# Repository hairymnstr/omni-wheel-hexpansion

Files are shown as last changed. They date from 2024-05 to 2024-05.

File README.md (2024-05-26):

# Motor Hexpansion / Omni Wheel Hexpansion

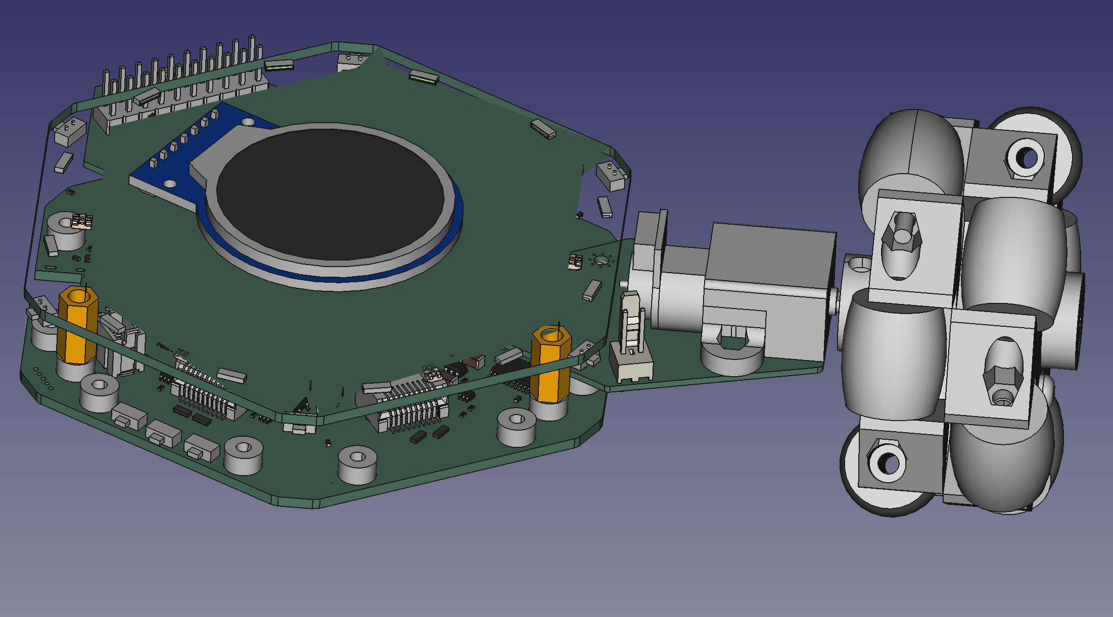
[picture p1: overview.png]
An omni wheel attached to a group of circuit boards all rendered in 3D CAD


This project is a "hexpansion" for the [EMF Camp Tildagon badge](https://tildagon.badge.emfcamp.org/).
It adds a motor driver, encoder reader and mounting points for an N20 motor.  The motor is mounted
straight out from the slot the hexpansion is mounted in.  By installing 3 of these hexpansions and
programming the badge appropriately you should be able to make it rotate or move in any direction
desired.

# Things you need to make a complete Omni Wheel Hexpansion

1. A Motor Hexpansion board as described in the kicad\_project folder
2. A 60mm Omni Wheel, see [my Omni Wheel repository](https://github.com/hairymnstr/OmniWheel) for a 3D printable design
3. A 110:1 geared micro metal motor with extended back shaft [COM0818 from Pimoroni](https://shop.pimoroni.com/products/micro-metal-gearmotor-extended-back-shaft?variant=39421592043603)
4. A long mounting bracket for the motor [COM0817 from Pimoroni](https://shop.pimoroni.com/products/long-micro-metal-gearmotor-bracket-pair?variant=39861109850195)
5. An encoder for the motor [PIM604 from Pimoroni](https://shop.pimoroni.com/products/micro-metal-motor-encoder?variant=39888423321683)
6. A JST-SH 6 way cable to connect the encoder/motor to the hexpansion [CAB1009 from Pimoroni](https://shop.pimoroni.com/products/jst-sh-cable-6-pin?variant=39292536455251)
7. A couple of short M2 bolts to secure the hexpansion to your badge [M2 x 5mm Torx Pan head bolt](https://www.westfieldfasteners.co.uk/Bolts_Screws_Metric/Torx_Pan_Screw_M2x5_A2_Stainless.html)

You'll need 3 of each part to make a complete hexpansion.

# Programming the hexpansion

To program a blank hexpansion I used the Raspberry Pi debug probe [(available from Pimoroni)](https://shop.pimoroni.com/products/raspberry-pi-debug-probe?variant=40511574999123).
The probe can be connected to both the SWD pins and the UART for test and debug.  The firmware
is also in this repository and can be built easily using Visual Studio Code or just by running
the Makefile provided you have an ARM embedded compiler installed.

# Hexpansion API

The hexpansion has a very simple interface, everything is controlled via I2C.

There are 2 devices presented (both in software on the STM32):

* 0x50 is a 256 byte fake EEPROM which has a valid "hexpansion" header identifying the board
* 0x42 has a register based control and status interface

Both devices operate in "memory" mode, i.e. they take an address then data to be read or written.
Both use single byte addressing.  Using the Micropython `readfrom_mem` and `writeto_mem` functions
will work.

There are only 2 registers defined, they can both be read and written, reading or writing any
other part of the 256 byte address space will be stored but won't make any difference to the
operation of the device.  Reads are guaranteed to be coherent so you won't get part of a register
that's updated between starting the I2C transaction and finishing it.

* Address 0, length 16 bit little endian: PWM value, a value in the range -100 to 100
* Address 2, length 16 bit little endian: Encoder position

Using the badge software you can use `machine.I2C` and `struct` to access these registers.
Note that on the Tildagon badge there are I2C buses for each hexpansion so you will need
to change the paramter to `I2C` for each slot you connect to.

This trivial example sets the speed to full reverse then prints out the current
encoder value.

    import struct
    import machine

    bus = machine.I2C(2)
    bus.writeto_mem(0x42, 0, struct.pack("<h", -100))
    print(struct.unpack("<h", bus.readfrom_mem(0x42, 2, 2))[0])

# Questions I think might be asked
## Why all the fuss about encoders?

Well originally I was planning a pen holding hexpansion as well and making a floor-turtle type
system.  To get any kind of accurate and repeatable motions I needed to know how far the wheels
were actually turning as there are variations between motors especially when under load.

## What's the point of the external MCU?

You could drive the motor driver and maybe do the encoder reading all from the MCU on the badge
itself.  But, I wanted to make sure I as catching all that encoder information on all three
motors.  To do that I decided a dedicated encoder controller would be good but couldn't find
one.  I also looked at using an I2C H-Bridge and adding an I2C EEPROM for board identification
and realised using one of the very cheap STM32G0 MCUs I could emulate an EEPROM and make an I2C
controlled motor driver and have a dedicated hardware encoder interface all in one.

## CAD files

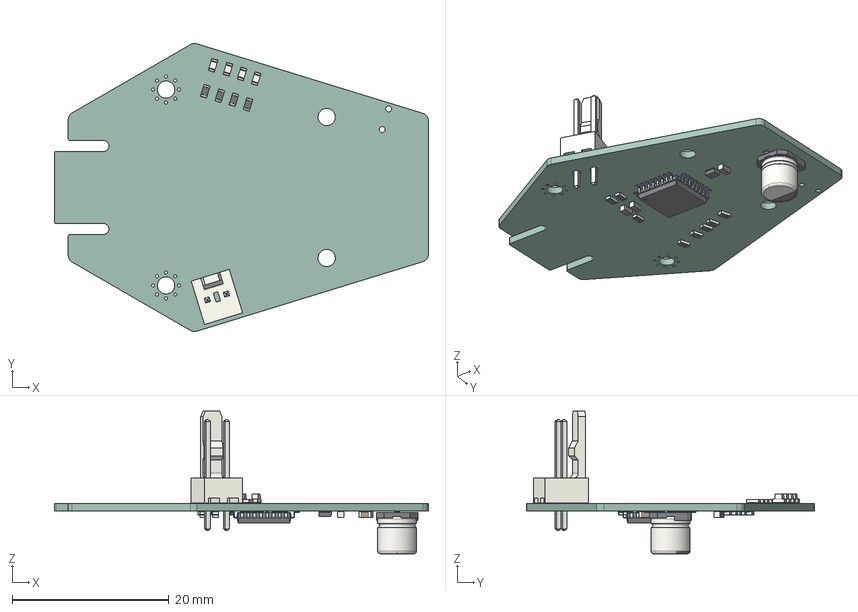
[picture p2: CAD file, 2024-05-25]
manufacturing/motor_hexpansion.step
47.8 x 36.8 x 18.2 mm
LED_0603_1608Metric x 4
R_0603_1608Metric x 12
Molex_AE_6410_02A
CP_Elec_5x54
LQFP_32_7x7mm_P08mm
C_0603_1608Metric x 4
SOT_563
motor_hexpansion_PCB

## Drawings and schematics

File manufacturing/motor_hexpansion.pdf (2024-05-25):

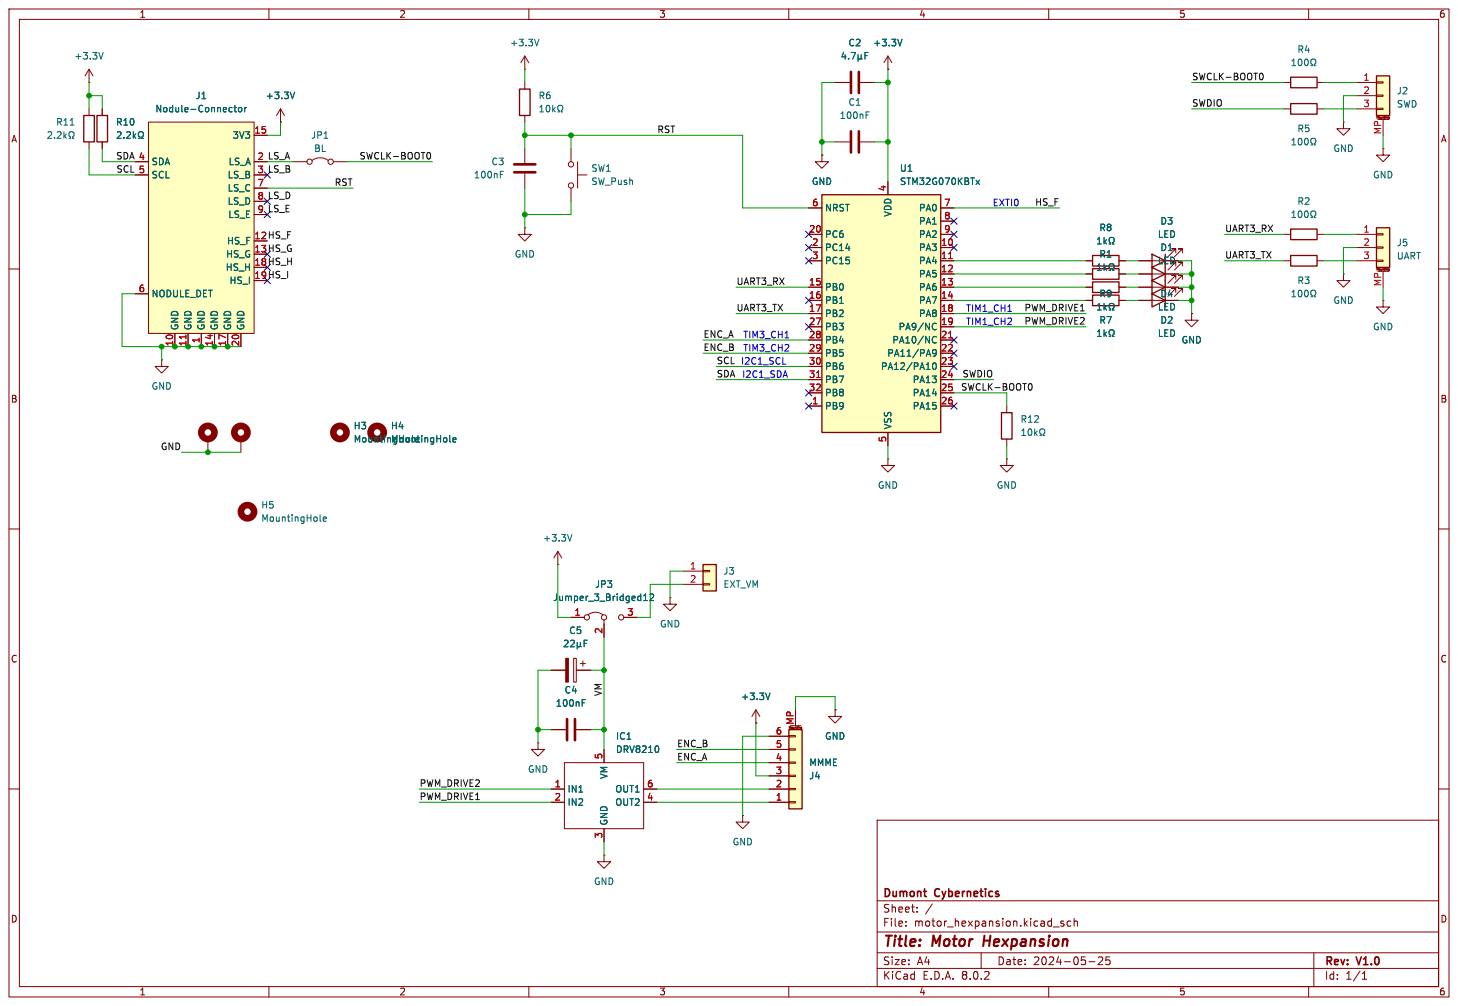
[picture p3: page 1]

File: motor_hexpansion.kicad_sch Sheet: / Dumont Cybernetics

Id: 1/1 Title: Motor Hexpansion

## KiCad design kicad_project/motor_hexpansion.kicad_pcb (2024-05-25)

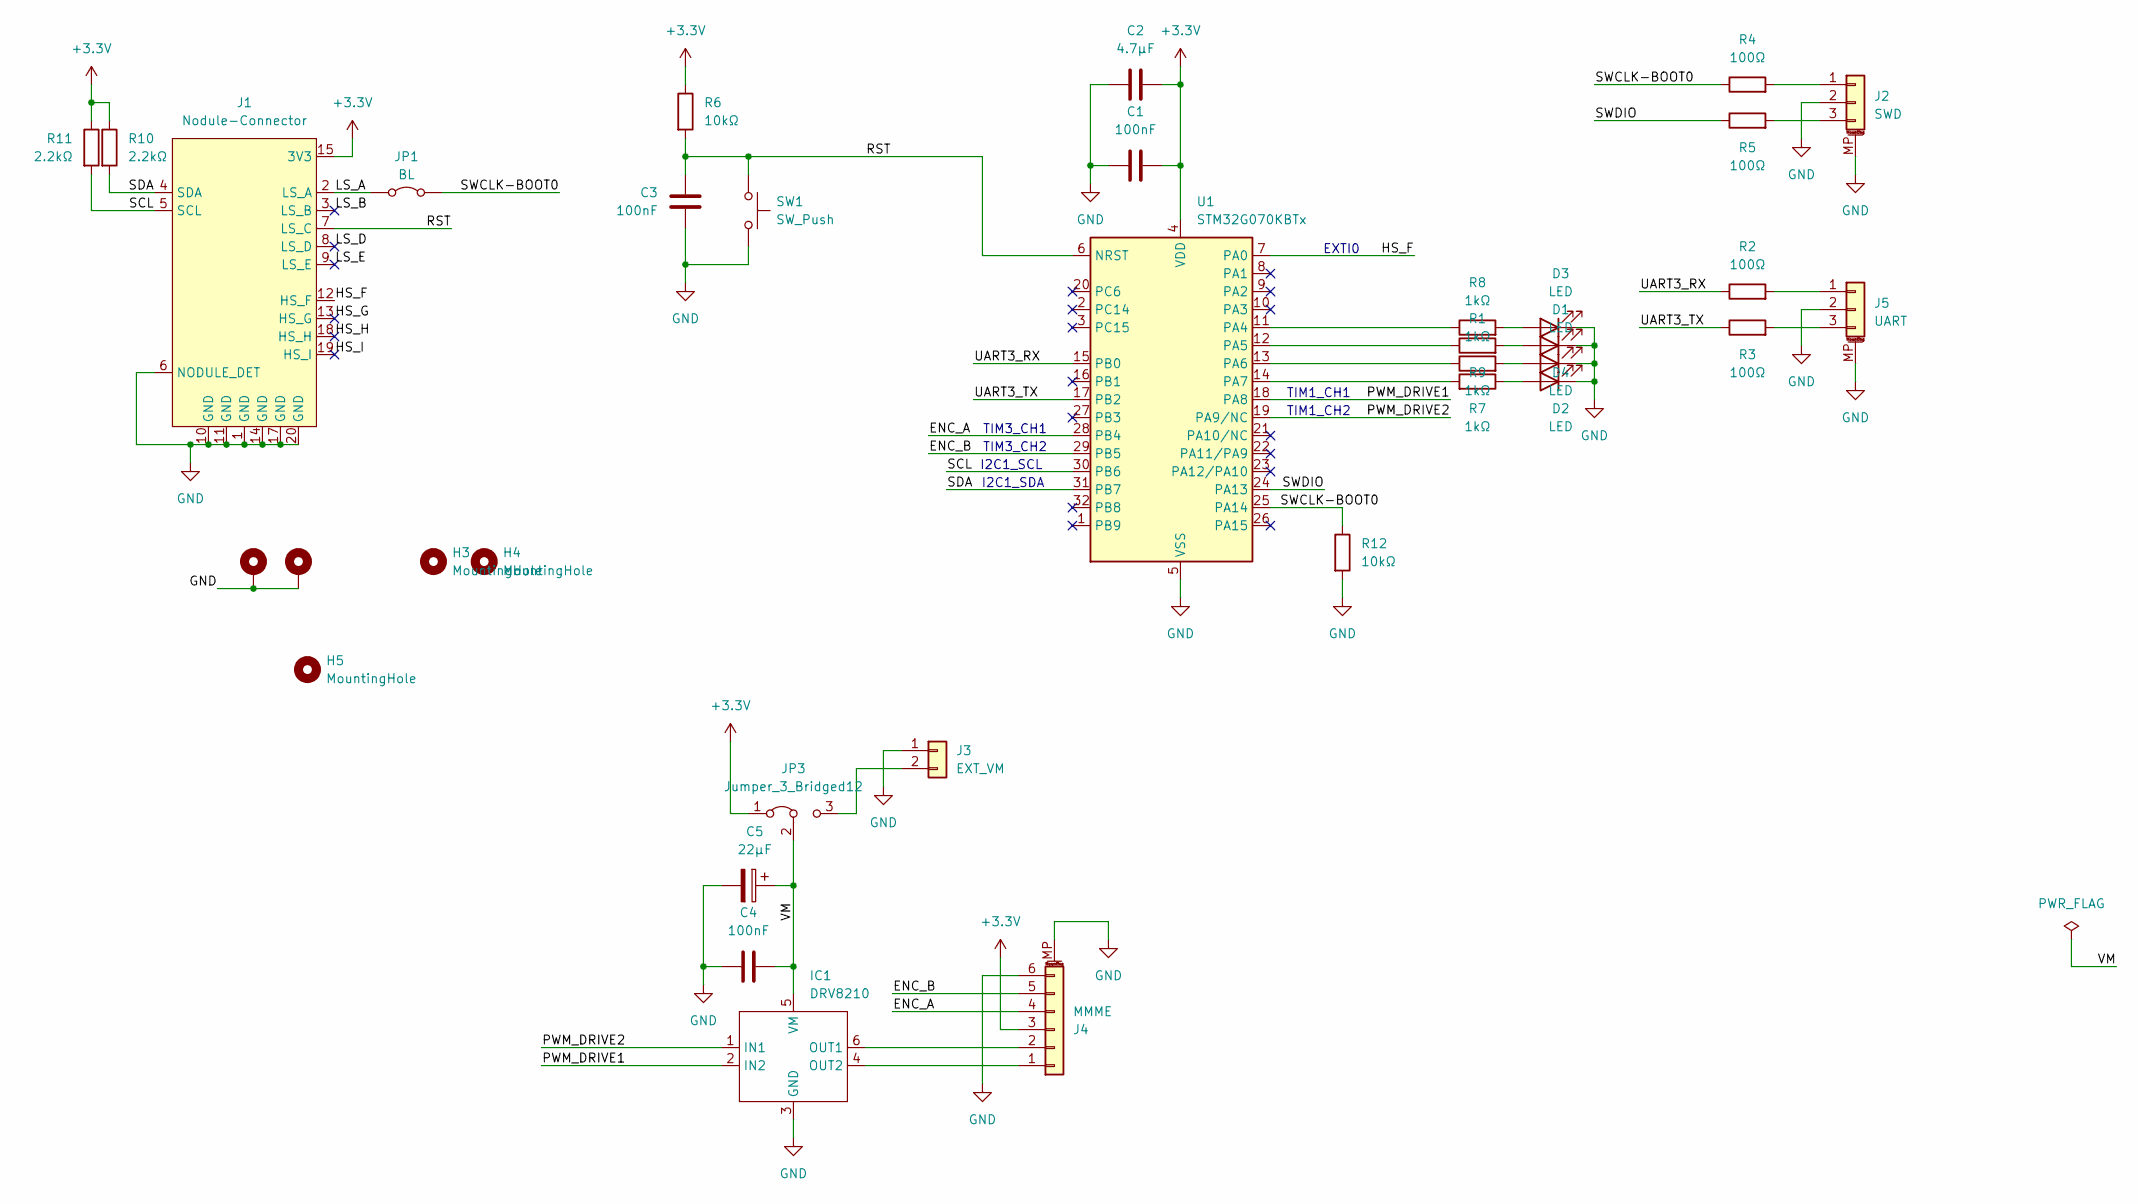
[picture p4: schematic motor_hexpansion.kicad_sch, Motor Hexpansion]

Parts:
C1, C3, C4: 100nF; C_0603_1608Metric
C2: 4.7µF; C_0603_1608Metric
C5: 22µF; CP_Elec_5x5.4
D1, D2, D3, D4: LED; LED_0603_1608Metric_Pad1.05x0.95mm_HandSolder
H1, H2: MountingHole_Pad; MountingHole_2.2mm_M2_Pad_Via
H3, H4: MountingHole; MountingHole_2.2mm_M2
H5: MountingHole; dclogo
IC1: DRV8210; SOT-563
J1: Nodule-Connector; nodule-edge-connector
J2: SWD; JST_SH_SM03B-SRSS-TB_1x03-1MP_P1.00mm_Horizontal
J3: EXT_VM; Molex_KK-254_AE-6410-02A_1x02_P2.54mm_Vertical
J4: MMME; JST_SH_SM06B-SRSS-TB_1x06-1MP_P1.00mm_Horizontal
J5: UART; JST_SH_SM03B-SRSS-TB_1x03-1MP_P1.00mm_Horizontal
JP1: BL; SolderJumper-2_P1.3mm_Bridged_Pad1.0x1.5mm
JP3: Jumper_3_Bridged12; SolderJumper-3_P1.3mm_Bridged2Bar12_Pad1.0x1.5mm_NumberLabe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
R1, R7, R8, R9: 1kΩ; R_0603_1608Metric
R2, R3, R4, R5: 100Ω; R_0603_1608Metric
R6, R12: 10kΩ; R_0603_1608Metric
R10, R11: 2.2kΩ; R_0603_1608Metric
SW1: SW_Push; Panasonic_EVQPUL_EVQPUC
U1: STM32G070KBTx; LQFP-32_7x7mm_P0.8mm

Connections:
+3.3V: C1.2, C2.2, J1.15 (3V3), J1.16 (3V3), J4.3, JP3.1 (A), R6.1, R10.1, R11.1, U1.4 (VDD)
/ENC_A: J4.4, U1.28 (PB4)
/ENC_B: J4.5, U1.29 (PB5)
/HS_F: J1.12 (HS_F), U1.7 (PA0)
/HS_G: J1.13 (HS_G)
/HS_H: J1.18 (HS_H)
/HS_I: J1.19 (HS_I)
/LS_A: J1.2 (LS_A), JP1.1 (A)
/LS_B: J1.3 (LS_B)
/LS_D: J1.8 (LS_D)
/LS_E: J1.9 (LS_E)
/PWM_DRIVE1: IC1.2 (IN2), U1.18 (PA8)
/PWM_DRIVE2: IC1.1 (IN1), U1.19 (PA9/NC)
/RST: C3.1, J1.7 (LS_C), R6.2, SW1.1, U1.6 (NRST)
/SCL: J1.5 (SCL), R11.2, U1.30 (PB6)
/SDA: J1.4 (SDA), R10.2, U1.31 (PB7)
/SWCLK-BOOT0: JP1.2 (B), R4.1, R12.1, U1.25 (PA14)
/SWDIO: R5.1, U1.24 (PA13)
/UART3_RX: R2.1, U1.15 (PB0)
/UART3_TX: R3.1, U1.17 (PB2)
/VM: C4.2, C5.1, IC1.5 (VM), JP3.2 (C)
GND: C1.1, C2.1, C3.2, C4.1, C5.2, D1.1 (K), D2.1 (K), D3.1 (K), D4.1 (K), H1.1, H2.1, IC1.3 (GND), J1.1 (GND), J1.6 (NODULE_DET), J1.10 (GND), J1.11 (GND), J1.14 (GND), J1.17 (GND), J1.20 (GND), J2.2, J2.MP (MountPin), J3.1, J4.6, J4.MP (MountPin), J5.2, J5.MP (MountPin), R12.2, SW1.2, U1.5 (VSS)
unnamed: D1.2 (A), R1.2
unnamed: D2.2 (A), R7.1
unnamed: D3.2 (A), R8.2
unnamed: D4.2 (A), R9.2
unnamed: IC1.6 (OUT1), J4.2
unnamed: IC1.4 (OUT2), J4.1
unnamed: J2.1, R4.2
unnamed: J2.3, R5.2
unnamed: J3.2, JP3.3 (B)
unnamed: J5.1, R2.2
unnamed: J5.3, R3.2
unnamed: R8.1, U1.11 (PA4)
unnamed: R9.1, U1.12 (PA5)
unnamed: R1.1, U1.13 (PA6)
unnamed: R7.2, U1.14 (PA7)

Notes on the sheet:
TIM1_CH2
EXTI0
I2C1_SDA
TIM1_CH1
I2C1_SCL
TIM3_CH1
TIM3_CH2

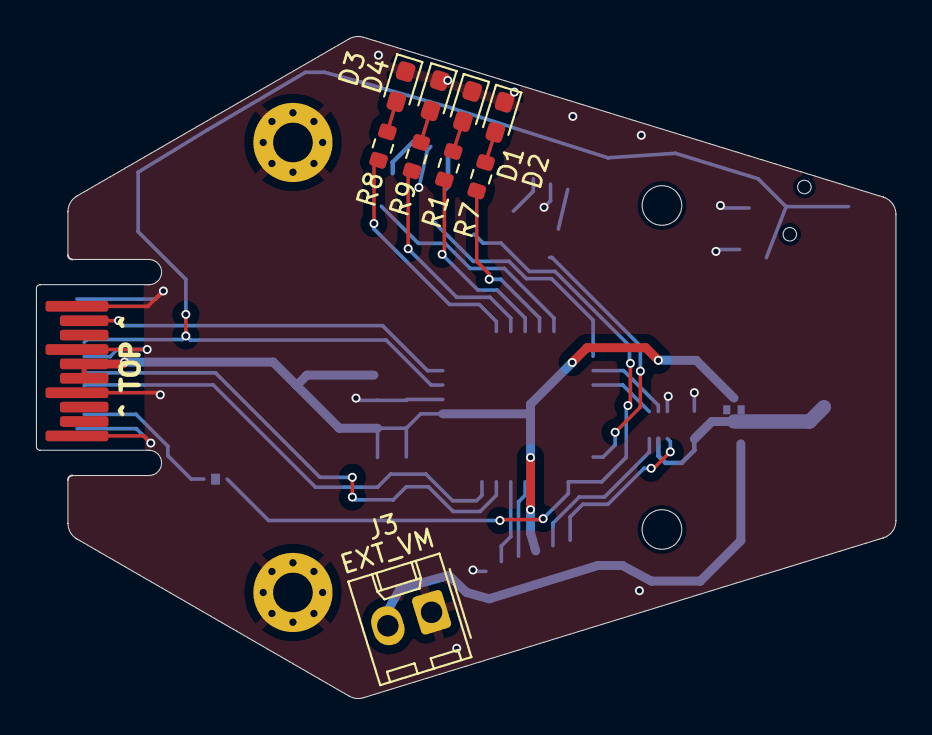
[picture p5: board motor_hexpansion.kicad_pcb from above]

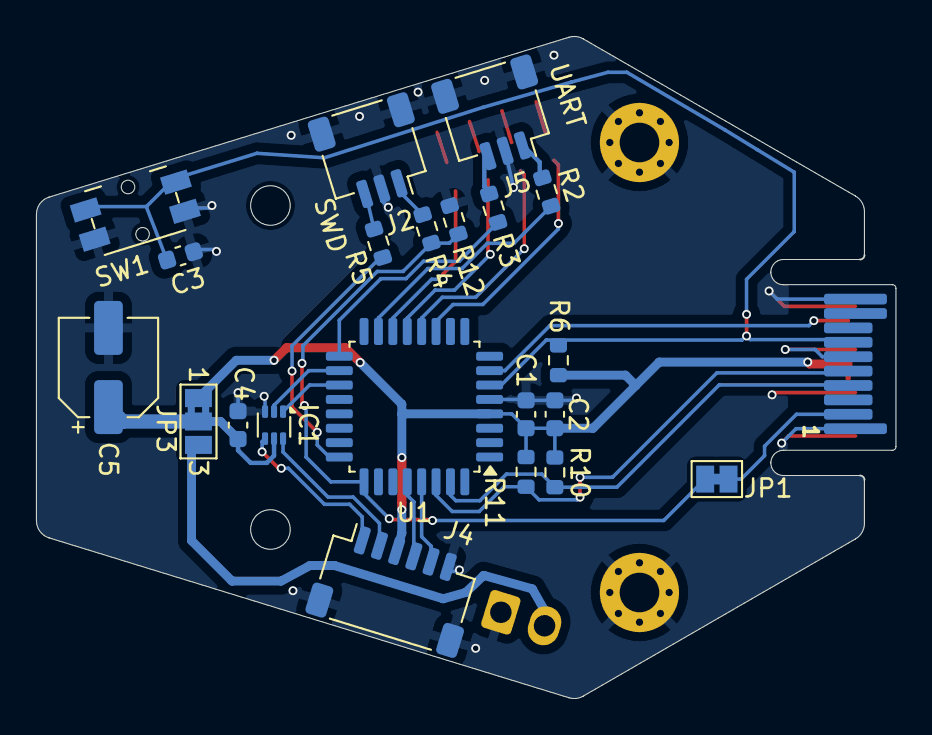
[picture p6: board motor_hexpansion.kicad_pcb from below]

Board: 2 copper layers, 47.8 x 36.8 mm, 35 parts (21 on the bottom side), 31 nets.

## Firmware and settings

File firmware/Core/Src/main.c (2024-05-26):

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
/* Includes ------------------------------------------------------------------*/
#include "main.h"
#include "cmsis_os.h"

/* USER CODE BEGIN Includes */

#include <stdbool.h>

#include "FreeRTOS.h"
#include "task.h"

#include "i2c_slave_state_machine.h"

/* USER CODE END Includes */

I2C_HandleTypeDef hi2c1;

TIM_HandleTypeDef htim1;
TIM_HandleTypeDef htim3;

UART_HandleTypeDef huart3;

osThreadId defaultTaskHandle;
osThreadId encoderTaskHandle;
void SystemClock_Config(void);
static void MX_GPIO_Init(void);
static void MX_I2C1_Init(void);
static void MX_TIM1_Init(void);
static void MX_TIM3_Init(void);
static void MX_USART3_UART_Init(void);
void StartDefaultTask(void const * argument);
void startEncoderTask(void const * argument);

/**
  * @brief  The application entry point.
  * @retval int
  */
int main(void)
{
  /* MCU Configuration--------------------------------------------------------*/

  /* Reset of all peripherals, Initializes the Flash interface and the Systick. */
  HAL_Init();

  /* Configure the system clock */
  SystemClock_Config();

  /* Initialize all configured peripherals */
  MX_GPIO_Init();
  MX_I2C1_Init();
  MX_TIM1_Init();
  MX_TIM3_Init();
  MX_USART3_UART_Init();
  /* USER CODE BEGIN RTOS_MUTEX */
  /* add mutexes, ... */
  /* USER CODE END RTOS_MUTEX */

  /* USER CODE BEGIN RTOS_SEMAPHORES */
  /* add semaphores, ... */
  /* USER CODE END RTOS_SEMAPHORES */

  /* USER CODE BEGIN RTOS_TIMERS */
  /* start timers, add new ones, ... */
  /* USER CODE END RTOS_TIMERS */

  /* USER CODE BEGIN RTOS_QUEUES */
  /* add queues, ... */
  /* USER CODE END RTOS_QUEUES */

  /* Create the thread(s) */
  /* definition and creation of defaultTask */
  osThreadDef(defaultTask, StartDefaultTask, osPriorityNormal, 0, 128);
  defaultTaskHandle = osThreadCreate(osThread(defaultTask), NULL);

  /* definition and creation of encoderTask */
  osThreadDef(encoderTask, startEncoderTask, osPriorityNormal, 0, 128);
  encoderTaskHandle = osThreadCreate(osThread(encoderTask), NULL);

  /* USER CODE BEGIN RTOS_THREADS */
  /* add threads, ... */
  /* USER CODE END RTOS_THREADS */

  /* Start scheduler */
  osKernelStart();

  /* We should never get here as control is now taken by the scheduler */
  /* Infinite loop */
  /* USER CODE BEGIN WHILE */
  while (1)
  {
    /* USER CODE END WHILE */

    /* USER CODE BEGIN 3 */
  }
  /* USER CODE END 3 */
}

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
/* USER CODE BEGIN 4 */
#define FORWARD 1
#define BACKWARD 2
int direction = 0;

void set_pwm(int8_t duty) {
  if (duty < -100) {
    duty = -100;
  }
  if (duty > 100) {
    duty = 100;
  }
  uint32_t extended_duty;
  if (duty < 0) {
    extended_duty = htim1.Init.Period * -1 * duty;
    htim1.Instance->CCR1 = extended_duty / 100;
    htim1.Instance->CCR2 = 0;
  } else {
    extended_duty = htim1.Init.Period * duty;
    htim1.Instance->CCR1 = 0;
    htim1.Instance->CCR2 = extended_duty / 100;
  }

}
/* USER CODE END 4 */

/* USER CODE BEGIN Header_StartDefaultTask */
/**
  * @brief  Function implementing the defaultTask thread.
  * @param  argument: Not used
  * @retval None
  */

 char print_buffer[128];
/* USER CODE END Header_StartDefaultTask */
void StartDefaultTask(void const * argument)
{
  /* USER CODE BEGIN 5 */
  /* Infinite loop */
  set_pwm(0);
  HAL_TIM_PWM_Start(&htim1, TIM_CHANNEL_1);
  HAL_TIM_PWM_Start(&htim1, TIM_CHANNEL_2);

  HAL_I2C_EnableListen_IT(&hi2c1);

  for(;;)
  {
    ulTaskNotifyTake(pdTRUE, portMAX_DELAY);

    // something happened to the registers, check if any of the input values were changed
    taskENTER_CRITICAL();
    uint8_t new_spd = regs[0];
    taskEXIT_CRITICAL();

    set_pwm(new_spd);
  }
  /* USER CODE END 5 */
}

/* USER CODE BEGIN Header_startEncoderTask */
/**
* @brief Function implementing the encoderTask thread.
* @param argument: Not used
* @retval None
*/
/* USER CODE END Header_startEncoderTask */
void startEncoderTask(void const * argument)
{
  /* USER CODE BEGIN startEncoderTask */
  HAL_TIM_Encoder_Start(&htim3, TIM_CHANNEL_ALL);
  /* Infinite loop */
  for(;;)
  {
    uint16_t enc_val = htim3.Instance->CNT;
    // update the registers in a critical section, and only if no I2C read
    // is going on so that the 16 bit value is always coherent
    taskENTER_CRITICAL();
    if (regs_locked == false) {
      regs[2] = enc_val >> 8;
      regs[3] = enc_val & 0xff;
    }
    taskEXIT_CRITICAL();
    osDelay(10);
  }
  /* USER CODE END startEncoderTask */
}

/**
  * @brief  Period elapsed callback in non blocking mode
  * @note   This function is called  when TIM16 interrupt took place, inside
  * HAL_TIM_IRQHandler(). It makes a direct call to HAL_IncTick() to increment
  * a global variable "uwTick" used as application time base.
  * @param  htim : TIM handle
  * @retval None
  */
void HAL_TIM_PeriodElapsedCallback(TIM_HandleTypeDef *htim)
{
  if (htim->Instance == TIM16) {
    HAL_IncTick();
  }
}

/**
  * @brief  This function is executed in case of error occurrence.
  * @retval None
  */
void Error_Handler(void)
{
  /* USER CODE BEGIN Error_Handler_Debug */
  /* User can add his own implementation to report the HAL error return state */
  __disable_irq();
  while (1)
  {
  }
  /* USER CODE END Error_Handler_Debug */
}

#ifdef  USE_FULL_ASSERT
/**
  * @brief  Reports the name of the source file and the source line number
  *         where the assert_param error has occurred.
  * @param  file: pointer to the source file name
  * @param  line: assert_param error line source number
  * @retval None
  */
void assert_failed(uint8_t *file, uint32_t line)
{
  /* USER CODE BEGIN 6 */
  /* User can add his own implementation to report the file name and line number,
     ex: printf("Wrong parameters value: file %s on line %d\r\n", file, line) */
  /* USER CODE END 6 */
}
#endif /* USE_FULL_ASSERT */

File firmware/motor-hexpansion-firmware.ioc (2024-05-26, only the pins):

Mcu.UserName=STM32G070KBTx
PA0.Signal=GPXTI0
PA13.Signal=SYS_SWDIO
PA14-BOOT0.Signal=SYS_SWCLK
PA4.GPIO_Label=LED0
PA4.Signal=GPIO_Output
PA5.GPIO_Label=LED1
PA5.Signal=GPIO_Output
PA6.GPIO_Label=LED2
PA6.Signal=GPIO_Output
PA7.GPIO_Label=LED3
PA7.Signal=GPIO_Output
PA8.Signal=S_TIM1_CH1
PA9.Signal=S_TIM1_CH2
PB0.Signal=USART3_RX
PB2.Signal=USART3_TX
PB4.Signal=S_TIM3_CH1
PB5.Signal=S_TIM3_CH2
PB6.Signal=I2C1_SCL
PB7.Signal=I2C1_SDA

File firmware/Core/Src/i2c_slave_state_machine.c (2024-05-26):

#include <stdlib.h>
#include <stdint.h>
#include <stdbool.h>
#include <stdio.h>

#include "FreeRTOS.h"
#include "queue.h"
#include "semphr.h"

#include "cmsis_os.h"
#include "main.h"
#include "i2c_slave_state_machine.h"

// emulated I2C EEPROM
extern const uint8_t eeprom[256];// = "THEX2024\x40\x00\x40\x00\x00\x00\x00\x00\xfe\xca\x34\x12\x00\x00OMNIWHL\x00\x00\x00";
// emulated registers
uint8_t regs[256];
bool regs_locked = false;

static uint8_t *dest;
static uint8_t offset; 	// index of current RAM cell
static uint8_t first=1;	// first byte --> new offset

extern osThreadId defaultTaskHandle;

void HAL_I2C_ListenCpltCallback(I2C_HandleTypeDef *hi2c)
{
	first = 1;
	HAL_I2C_EnableListen_IT(hi2c); // slave is ready again
}

void HAL_I2C_AddrCallback(I2C_HandleTypeDef *hi2c, uint8_t TransferDirection, uint16_t AddrMatchCode)
{
	HAL_GPIO_WritePin( LED1_GPIO_Port, LED1_Pin, GPIO_PIN_SET );
    if ((AddrMatchCode >> 1) == 0x50) {
        dest = eeprom;
    } else {
        dest = regs;
        regs_locked = true;
    }
	if( TransferDirection==I2C_DIRECTION_TRANSMIT ) {
		if( first ) {
            HAL_I2C_Slave_Seq_Receive_IT(hi2c, &offset, 1, I2C_NEXT_FRAME);
		} else {
            if (dest == regs) {
    			HAL_I2C_Slave_Seq_Receive_IT(hi2c, &dest[offset], 1, I2C_NEXT_FRAME);
            } else {
                __HAL_I2C_GENERATE_NACK(hi2c);  // EEPROM is read only
            }
		}
	} else {
		HAL_I2C_Slave_Seq_Transmit_IT(hi2c, &dest[offset], 1, I2C_NEXT_FRAME);
	}
	HAL_GPIO_WritePin( LED1_GPIO_Port, LED1_Pin, GPIO_PIN_RESET );
}

void HAL_I2C_SlaveRxCpltCallback(I2C_HandleTypeDef *hi2c)
{
	HAL_GPIO_WritePin( LED2_GPIO_Port, LED2_Pin, GPIO_PIN_SET );
	if(first) {
		first = 0;
	} else {
		offset++;
	}
    if (dest == regs) {
    	HAL_I2C_Slave_Seq_Receive_IT(hi2c, &dest[offset], 1, I2C_NEXT_FRAME);
    } else {
        __HAL_I2C_GENERATE_NACK(hi2c);  // EEPROM is read only
    }
	HAL_GPIO_WritePin(LED2_GPIO_Port, LED2_Pin, GPIO_PIN_RESET );
}

void HAL_I2C_SlaveTxCpltCallback(I2C_HandleTypeDef *hi2c)
{
	HAL_GPIO_WritePin( LED2_GPIO_Port, LED2_Pin, GPIO_PIN_SET );
	offset++;
	HAL_I2C_Slave_Seq_Transmit_IT(hi2c, &dest[offset], 1, I2C_NEXT_FRAME);
	HAL_GPIO_WritePin( LED2_GPIO_Port, LED2_Pin, GPIO_PIN_RESET );
}

void HAL_I2C_ErrorCallback(I2C_HandleTypeDef *hi2c)
{
	HAL_GPIO_WritePin( LED3_GPIO_Port, LED3_Pin, GPIO_PIN_SET );
	if( HAL_I2C_GetError(hi2c)==HAL_I2C_ERROR_AF ) {
		// transaction terminated by master
		offset--;
        regs_locked = false;
        xTaskNotify(defaultTaskHandle, 0, 0);
	}
	HAL_GPIO_WritePin( LED3_GPIO_Port, LED3_Pin, GPIO_PIN_RESET );
}

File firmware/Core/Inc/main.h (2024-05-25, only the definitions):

#define LED0_Pin GPIO_PIN_4
#define LED0_GPIO_Port GPIOA
#define LED1_Pin GPIO_PIN_5
#define LED1_GPIO_Port GPIOA
#define LED2_Pin GPIO_PIN_6
#define LED2_GPIO_Port GPIOA
#define LED3_Pin GPIO_PIN_7
#define LED3_GPIO_Port GPIOA

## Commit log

2024-05-25 Adding files to version control for sharing
    [motor_hexpansion.kicad_pcb, motor_hexpansion.kicad_sch, motor_hexpansion.step]
2024-05-26 Made the I2C interface work. Needs more eeprom work

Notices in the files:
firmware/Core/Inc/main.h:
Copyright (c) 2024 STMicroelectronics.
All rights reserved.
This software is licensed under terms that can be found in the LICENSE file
